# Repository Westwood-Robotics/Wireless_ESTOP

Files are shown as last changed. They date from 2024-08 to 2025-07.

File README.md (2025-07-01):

# Wireless ESTOP Lite
Wireless ESTOP that works with BEAR actuators

This repo currently contains：\
**Rev1:** The open-source code for the transmitter and receiver of the Rev1 version of our Wireless ESTOP Lite system, which uses RP2040 as its MCU and NRF24 for 2.4GHz wireless communication;\
**Rev2:** The binary code of the remote transmitter and the receiver, code for changing settings of the modules, and the schematic of the Wireless ESTOP Lite modules.

## Licensing
The Wireless ESTOP is dual-licensed under both commercial and open-source licenses. The work in this repo is under GNU General Public License (GPL) version 3, which is ideal for use cases such as open-source projects with open-source distribution, student/academic purposes, hobby projects, internal research projects without external distribution, or other projects where all GPL obligations can be met. Read the full text of [the GNU GPL version 3](https://www.gnu.org/licenses/gpl-3.0.html) for details.  
Contact us for commercial license should you need full rights to create and distribute the platform on your own terms without any open-source license obligations.

## Upload and update
All modules are loaded with most recent version(at the time of shipping) of the software. When a flash or update is needed, simply connect the module to your computer while holding down the BOOT button then a new drive should pop up. 

Download then Drag and drop the corresponding .uf2 file into the drive to finish the upload.

## Receiver Features
### Buttons, Indicators and Pinout on Receiver
The RGB indicator flashes in blue when a signal disturbance is detected. The three indicators on the right shows the status of ESTOP, transmitter connection and power status of the receiver module. \
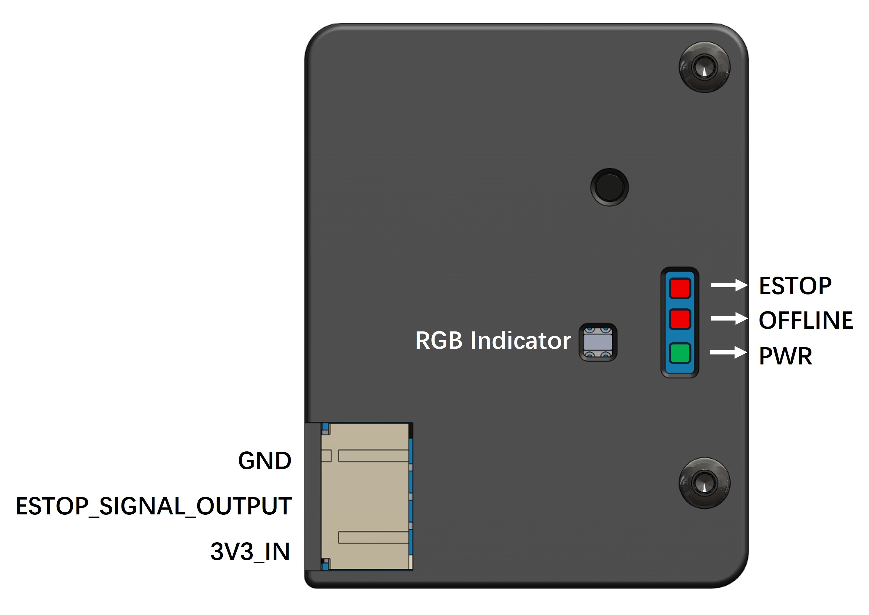
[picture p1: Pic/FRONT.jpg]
\
Connect the **ESTOP_SIGNAL_OUTPUT** pin and the **GND** pin on the PH 2mm 3Pin port respectively to the ESTOP and GND channel on your BEAR bus. \
You can also use the **3V3_IN** pin to power the receiver module, but you need to connect the ***EXT_3V3*** jumper on the top side of the board with solder. \
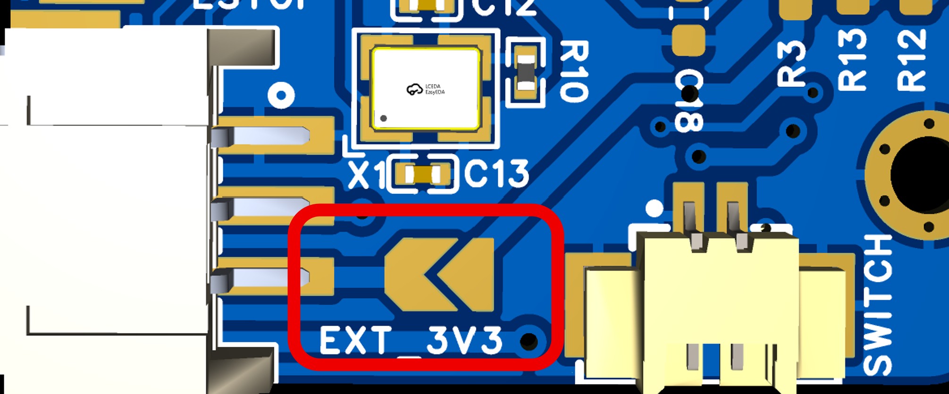
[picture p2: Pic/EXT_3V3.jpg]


Connect the two terminals on your ESTOP swith(NC switch) to the **ESTOP_SWITCH** pin and the **GND** pin on the 1.25mm 2Pin port. You can power the board by connecting the **5V** pin and the **GND** pin to a 5V power supply. \
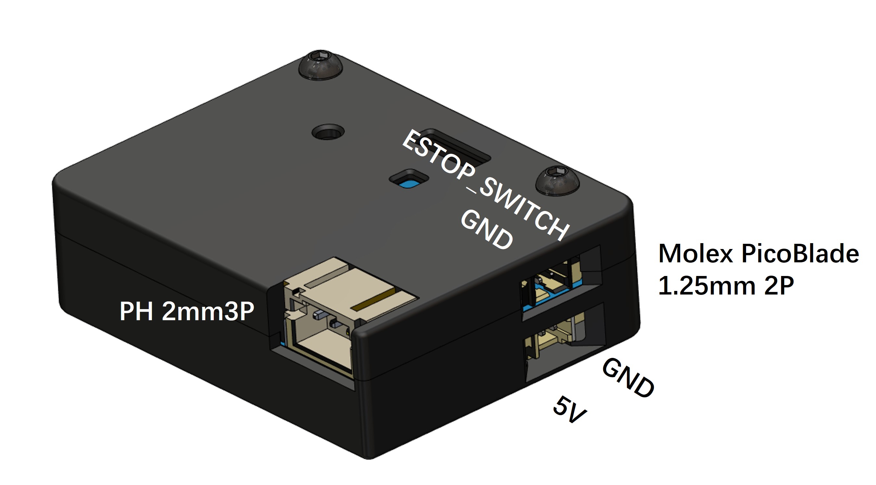
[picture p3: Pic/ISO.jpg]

> [!CAUTION]
> Only power the board with a single source. Avoid co-existance of power supply from 3V3, 5V and the USB-C port.

When working with a bus that has different series of BEAR actuators, it is recommended to use the BJT on the receiver module for stable ESTOP control, and the jumper on the bottom of the board should be modified accordingly. When the BJT is not used(by default) the ***Direct*** terminal should be connected to the center pad, and if the BJT is used, the ***CTRL*** terminal should be connected to the center pad:\
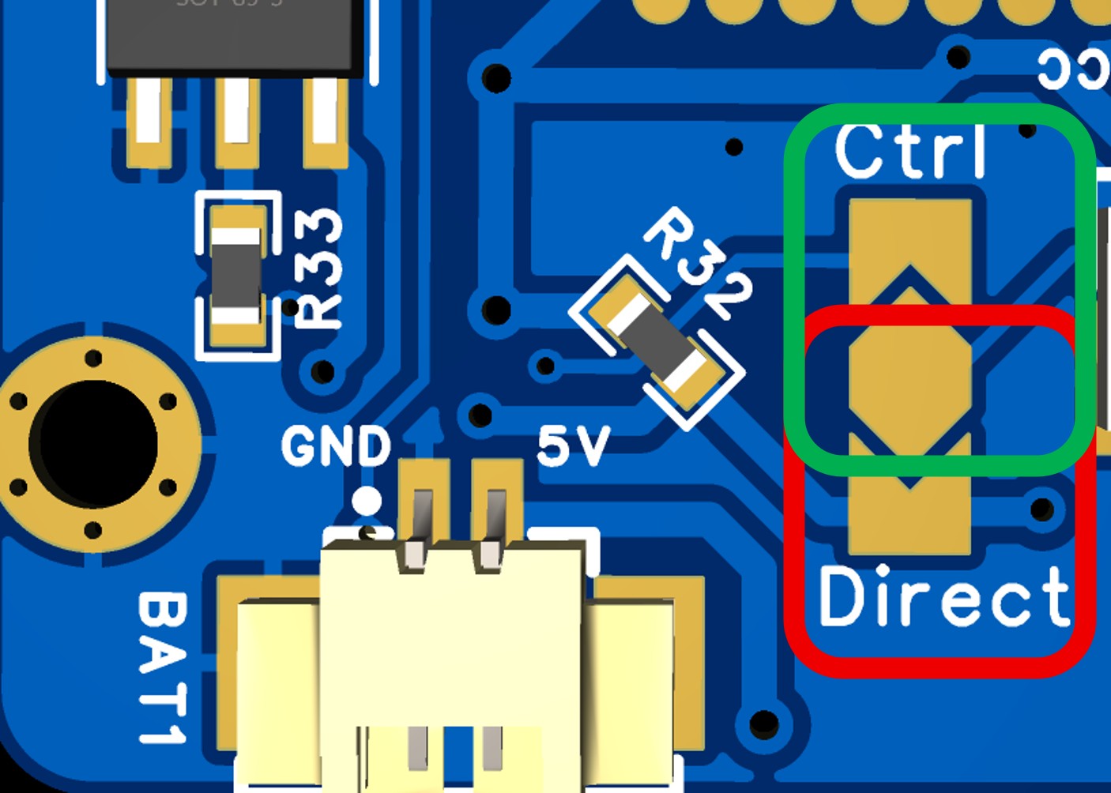
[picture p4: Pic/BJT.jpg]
\
**See below for how to write BJT settings to the RX module.**
> [!Note]
> Make sure you have the correct BJT setting in the software.

## Wireless ESTOP Channel and BJT Setup
To avoid communication conflict between multiple Wireless ESTOP systems, users can now modify their communication channel setup.
### Instructions
1. Identify the serial port name for you Wireless ESTOP device (transmitter/receiver). Plug in the device and enter the following command in terminal:
    ```bash
    ls /dev/serial/by-id
    ```
2. Press the ESTOP button and run the program.
    ```bash
    ./setup
    ```
4. Enter the serial port name.
5. Wait for the connection and then **follow the instruction**. 
6. You need to have the same channel setup for your transmitter and receiver.

## Further DIY
### Scheme
Feel free to develop upon the hardware of the Rev2 modules. The transmitter and receiver shares the same hardware and the schematic drawing is [here](https://github.com/Westwood-Robotics/Wireless_ESTOP/blob/Rev2/SCH_WirelessESTOP_Lite_2025-06-10.pdf)
### ARDUINO IDE
To work with the RP2040 on the Wireless ESTOP modules, please first config your ARDUINO IDE with Raspberry Pi Pico setup: https://github.com/earlephilhower/arduino-pico

## 3D Model
RX Module(Receiver): https://github.com/Westwood-Robotics/Wireless_ESTOP/blob/main/ESTOP_Lite/Rev0/Dummy/ESTOP_RX.STEP

## Update Log:Rev1->Rev2
1. Pin change: the following two pins has been moved: <br />
   NRF_CE -> 19<br />
   SPI0_CSN -> 5<br />
2. Add support for one additional SPI line, pins can also be used for general purposes. (scheme/drawing to be released)
3. ESTOP signal can be sent directly or via a BJT. Select it on the board then modify the code.
4. Change settings and IDs by writting to EEPROM.

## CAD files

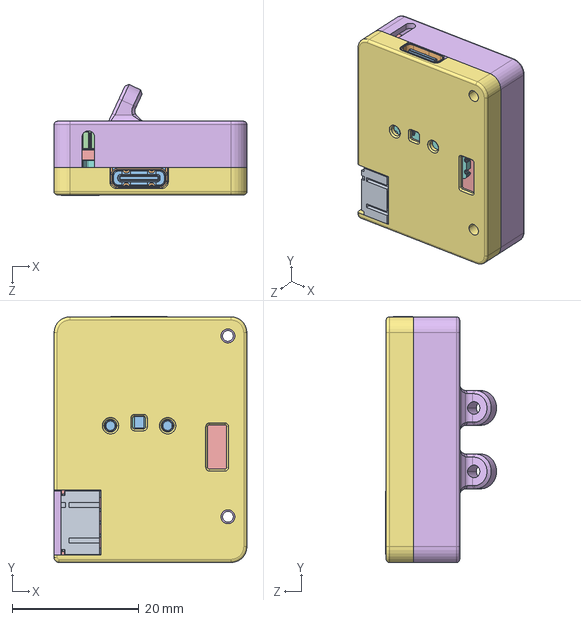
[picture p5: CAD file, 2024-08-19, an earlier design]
ESTOP_Lite/Rev1/Dummy/ESTOP_RX.STEP
30.4 x 38.8 x 17.5 mm

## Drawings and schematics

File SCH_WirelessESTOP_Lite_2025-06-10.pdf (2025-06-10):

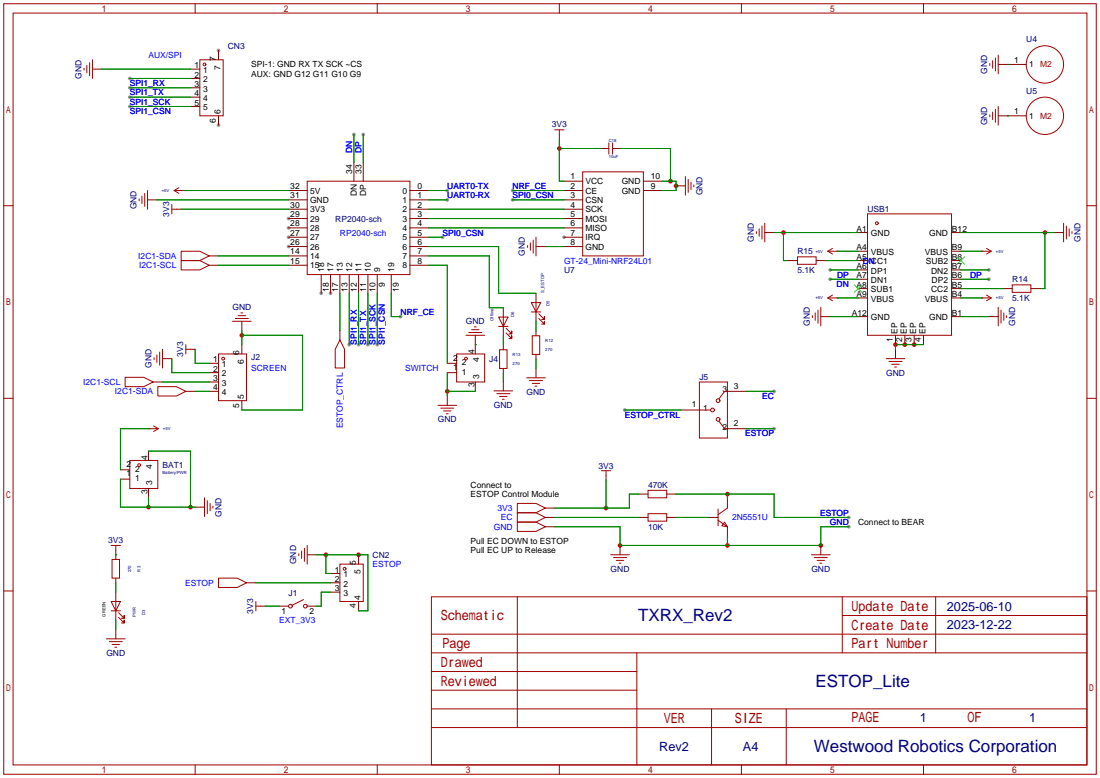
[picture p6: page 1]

SPI-1: GND RX TX SCK ~CS
AUX: GND G12 G11 G10 G9

Connect to
ESTOP Control Module
GND
Pull EC DOWN to ESTOP
Pull EC UP to Release

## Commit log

2024-08-19 Language standardized.
    [ESTOP_RX.STEP]
2025-06-06 Add Wireless ESTOP System Channel Setup Instruction please refer to README.md in Util
2025-06-10 Update pictures
    [ESTOP_RX.STEP]
